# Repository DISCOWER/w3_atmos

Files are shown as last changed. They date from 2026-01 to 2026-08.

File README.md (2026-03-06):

---
layout: home
title: DISCOWER ATMOS
permalink: /
---

Welcome to the DISCOWER Autonomy Testbed for Multi-purpose Orbiting Systems (ATMOS) documentation page. 

ATMOS is a free-flyer platform developed at the KTH Space Robotics Laboratory for testing and validating space systems. The platform is composed by an air-bearing support system for frictionless motion, a modular actuation plate compatible with solenoid thrusters and propeller-based actuation, and a payload support system for testing various accessories. ATMOS aims at being a state-of-the-art platform for space robotics testing and validation, with the aim of reducing ground-to-orbit testing costs and increasing the reliability of space systems.

<html>
<script type="module" src="https://unpkg.com/@google/model-viewer/dist/model-viewer.min.js"></script>
<model-viewer src="/3D/full_assy_wAttachments.glb" 
              alt="A 3D model" 
              ar 
              auto-rotate 
              camera-controls 
              shadow-intensity="1">
</model-viewer>
<style>
    model-viewer {
        width: 100%;
        height: 500px;
        background-color: var(background-color, #ffffff);
    }
</style>
</html>

Here you can see the 3D platform used in DISCOWER. In this website, we provide detailed setups on assembling such a free-flyer platform, including modular actuation plates and payload bays.

> ##### ATMOS in Augmented Reality
>
> Visualizing this website on Android allows you to see ATMOS in Augmented Reality. Just click the AR button on the 3D model above!
{: .block-tip }

### Changelog
The latest changes to the documentation can be found below:
- **2026-03-06**: 
  - Added MIT and UIUC to ATMOS-supported institutions
  - Updated Bill-of-Materials part 0212 with the correct version of the Festo Push-in T-connector (QSMT-6 instead of QST-6)
- **2026-02-19**:
  - Contributions from Caltech (Vivian Norum and Teagan Abeling) and MIT (Kareena Shah and Brooke Schmelz): 
    - Updated regulator part number for thruster module.
    - Updated baseplate aluminum profile height from 21cm to 23cm for extra clearance for thicker bottles
    - Added missing item on BOM (air-bearing to push-in tubing adapter)
- **2025-01-15**:
  - ATMOS website is now open-source! Feel free to send in Pull-Requests with updates to the documentation at [https://github.com/DISCOWER/w3_atmos](https://github.com/DISCOWER/w3_atmos)

- **2025-11-24**: 
  - Updated Jetson Box STL files in [Avionics Plate](https://atmos.discower.io/jekyll/2024-11-23-avionics.html#onboard-computer) to match latest version of ATMOS
  - Added aluminium profile height for each layer in [Base Plate](https://atmos.discower.io/jekyll/2024-11-21-baseplate.html#pneumatic-plate---attached), [Actuation Plate](http://127.0.0.1:4000/jekyll/2024-11-22-actuation.html#aluminium-profiles), and [Avionics Plate](https://atmos.discower.io/jekyll/2024-11-23-avionics.html#payload-aluminium-profiles)
  - Updated PX4 instructions in [Pixhawk Setup](https://atmos.discower.io/pages/PX4/) for the multiple connection options with UXRCE and MAVLink

## Citing this work

A preprint with information regarding ATMOS and the KTH Space Robotics Laboratory is [available on arXiv](https://arxiv.org/abs/2501.16973), with the latest version being published in [IEEE Transactions on Field Robotics](https://ieeexplore.ieee.org/document/11245595). If this work is useful for your research, consider citing:

```bibtex
@ARTICLE{11245595,
  author={Roque, Pedro and Phodapol, Sujet and Krantz, Elias and Lim, Jaeyoung and Verhagen, Joris and Jiang, Frank J. and Dörner, David and Mao, Huina and Tibert, Gunnar and Siegwart, Roland and Stenius, Ivan and Tumova, Jana and Fuglesang, Christer and Dimarogonas, Dimos V.},
  journal={IEEE Transactions on Field Robotics}, 
  title={Toward Open-Source and Modular Space Systems With ATMOS}, 
  year={2026},
  volume={3},
  number={},
  pages={141-161},
  keywords={Space vehicles;Robots;Hardware;Floors;Testing;Aerospace electronics;Attitude control;Orbits;MATLAB;Propulsion;Multirobot systems;orbital robotics},
  doi={10.1109/TFR.2025.3632772}}
```
<html>
<iframe src="https://drive.google.com/file/d/1IQ3zcbxwNgNY_v_4YbrNEkiCZEV_he8L/preview" width="100%" height="435" allow="autoplay"></iframe>
</html>

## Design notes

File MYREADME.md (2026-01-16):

# platform
This repository provides an open-source free-flyer platform for testing satellite-like dynamics in ground testbeds.

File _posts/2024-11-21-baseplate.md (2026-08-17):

---
title: Base Plate
author: Pedro Roque
date: 2024-11-21
category: Jekyll
layout: post
---

To assemble a free-flyer, we will start with the bottom plate. This plate provides support for the remaining layers and contains the pneumatic components for air-supply, regulation, as well as air bearings for frictionless motion. The final assembly can be seen in the 3D model below.

<html>

<script type="module" src="https://unpkg.com/@google/model-viewer/dist/model-viewer.min.js"></script>
<model-viewer src="/3D/1. Bottom Plate/1_f.glb" 
              alt="Bottom plate" 
              ar 
              auto-rotate 
              camera-controls 
              shadow-intensity="1">
</model-viewer>
<style>
    model-viewer {
        width: 100%;
        height: 500px;
        background-color: var(background-color, #ffffff);
    }
</style>
</html>

## Polycarbonate Plate

The baseplate is composed of a single 8 mm thick polycarbonate plate - item 0101 in the Bill of Materials. The diameter of the plate is 400mm and it is recommended to be cut using a CNC waterjet. The DXF file for the plate can be downloaded [here](/dxf/base_plate.DXF), and the end result can be seen in the 3D model below.

<html>
<script type="module" src="https://unpkg.com/@google/model-viewer/dist/model-viewer.min.js"></script>
<model-viewer src="/3D/1. Bottom Plate/1_a.glb" 
              alt="Bottom plate - PC" 
              ar 
              auto-rotate 
              camera-controls 
              shadow-intensity="1">
</model-viewer>
<style>
    model-viewer {
        width: 100%;
        height: 500px;
        background-color: var(background-color, #ffffff);
    }
</style>
</html>

<div style="display: table; width: 300px; margin: 20px auto; border: 2px solid #000000; padding: 10px; text-align: center; background-color: var(background-color, #ffffff); border-radius: 4px;">
  Download the <a href="/dxf/base_plate.DXF" download>DXF file</a>.
</div>

## Air Bearings

With the plate cut, we are ready to start attaching the air bearings. These bearings are used to provide a frictionless motion to the platform. The bearings are attached to the plate using the provided mounting screws, nuts and washers - items 0103 and 0104. In the center of the plate, on the underside, we should also attach an X-connecting piece to allow for the air supply to reach the bearings - item 0214. Then, connect the air bearings to the X-connector using 6mm tubing - item 0210. A further length of tubing runs from the X-connector up to the topside of the plate, where it connects to the air bearings regulator - item 0206 - in the step below. The 3D model below shows only the placement of the bearings and X-connector; the tubing runs and regulator (0206) not depicted.

<html>
<script type="module" src="https://unpkg.com/@google/model-viewer/dist/model-viewer.min.js"></script>
<model-viewer src="/3D/1. Bottom Plate/1_b.glb" 
              alt="Bottom plate - PC" 
              ar 
              auto-rotate 
              camera-controls 
              shadow-intensity="1">
</model-viewer>
<style>
    model-viewer {
        width: 100%;
        height: 500px;
        background-color: var(background-color, #ffffff);
    }
</style>
</html>

> ##### NOTE
>
> After installation, the air bearings shall be protected from damage and kept on clean surfaces.
> We recommend to use the provided boxes for storage and transportation.
{: .block-tip }

## Bottle Supports and Regulators

At this stage, we are ready to install the bottle supports, thruster pressure regulator, and air bearings regulator. The first step is to print all the 3D supports in [here](/stl/pneumatic_mount/base_plate_prints.zip). The parts are then attached to the plate using M4x20 mm screws, nuts and washers according to the 3D model below. The items used in this step are 0206, 0207, 0208. The air bearings regulator - item 0206 - takes the tubing run coming up from the X-connector beneath the plate. For the thruster pressure regulator - item 0207 - screw a push-in fitting - item 0208 - into the inlet and outlet ports and tighten each with a wrench before connecting any tubing; the G1/4 thread seals against the port face, and leaving these hand-tight is a common source of air leaks. The 6mm tubing then presses into the fittings by hand.

<html>
<script type="module" src="https://unpkg.com/@google/model-viewer/dist/model-viewer.min.js"></script>
<model-viewer src="/3D/1. Bottom Plate/1_c.glb" 
              alt="Bottom plate - PC" 
              ar 
              auto-rotate 
              camera-controls 
              shadow-intensity="1">
</model-viewer>
<style>
    model-viewer {
        width: 100%;
        height: 500px;
        background-color: var(background-color, #ffffff);
    }
</style>
</html>
<div style="display: table; width: 300px; margin: 20px auto; border: 2px solid #000000; padding: 10px; text-align: center; background-color: var(background-color, #ffffff); border-radius: 4px;">
  Download the <a href="/stl/pneumatic_mount/base_plate_prints.zip" download>STL files</a>.
</div>

## Bottles and in-line Regulators

Next, we are ready to test the bottles' mounting and install all in-line regulators. Start by taking one bottle (item 0201) and attach to it the first (item 0202) and second (item 0203) regulators. Then, at the end of the last regulator, make sure to use the provided Festo-compatible fitting. Lastly, attach the 3D print part that secures the regulators to the bottle next holder.

<html>
<script type="module" src="https://unpkg.com/@google/model-viewer/dist/model-viewer.min.js"></script>
<model-viewer src="/3D/1. Bottom Plate/1_d.glb" 
              alt="Bottom plate - PC" 
              ar 
              auto-rotate 
              camera-controls 
              shadow-intensity="1">
</model-viewer>
<style>
    model-viewer {
        width: 100%;
        height: 500px;
        background-color: var(background-color, #ffffff);
    }
</style>
</html>

## Aluminium Profiles

Almost at the last step, we are now ready to install the supporting aluminium profiles. These profiles are used to provide structural support to the platform and are attached to the plate using the provided angle brackets and T-slot nuts. The items used in this step are 0102, 0105, 0106. M4×8 mm screws and nuts are used to secure these items to the locations shown in the 3D model below. Attach the angle brackets - item 0105 - to the profiles first, working on a level surface: leave the T-slot nuts loose enough to slide, square everything up, then tighten evenly. Brackets set slightly off-square here will leave the profiles uneven once mounted to the polycarbonate plate.

<html>
<script type="module" src="https://unpkg.com/@google/model-viewer/dist/model-viewer.min.js"></script>
<model-viewer src="/3D/1. Bottom Plate/1_e.glb" 
              alt="Bottom plate - PC" 
              ar 
              auto-rotate 
              camera-controls 
              shadow-intensity="1">
</model-viewer>
<style>
    model-viewer {
        width: 100%;
        height: 500px;
        background-color: var(background-color, #ffffff);
    }
</style>
</html>

## Manifold

### Manifold - Assembly

At this point, we are ready to assemble the manifold plate that will direct the air from from the bottles to the air bearings and actuators. The STL files used in this step can be found below.

<html>
<script type="module" src="https://unpkg.com/@google/model-viewer/dist/model-viewer.min.js"></script>
<model-viewer src="/3D/3.1 Manifold/3_1_d.glb" 
              alt="Bottom plate - PC" 
              ar 
              auto-rotate 
              camera-controls 
              camera-orbit="180deg 75deg 3m" 
              shadow-intensity="1">
</model-viewer>
<style>
    model-viewer {
        width: 100%;
        height: 500px;
        background-color: var(background-color, #ffffff);
    }
</style>
</html>

<div style="display: table; width: 300px; margin: 20px auto; border: 2px solid #000000; padding: 10px; text-align: center; background-color: var(background-color, #ffffff); border-radius: 4px;">
  Download the <a href="/stl/control_panel/control_panel.zip" download>STL files</a>.
</div>

### Manifold - Baseplate

First, start by 3D printing the baseplate.

<html>
<script type="module" src="https://unpkg.com/@google/model-viewer/dist/model-viewer.min.js"></script>
<model-viewer src="/3D/3.1 Manifold/3_1_a.glb" 
              alt="Bottom plate - PC" 
              ar 
              auto-rotate 
              camera-controls 
              camera-orbit="180deg 75deg 3m" 
              shadow-intensity="1">
</model-viewer>
<style>
    model-viewer {
        width: 100%;
        height: 500px;
        background-color: var(background-color, #ffffff);
    }
</style>
</html>

### Manifold - Supports

Then, we attach the 3D printed supports for the valves and tubing using M3x8 mm screws and nuts.

<html>
<script type="module" src="https://unpkg.com/@google/model-viewer/dist/model-viewer.min.js"></script>
<model-viewer src="/3D/3.1 Manifold/3_1_b.glb" 
              alt="Bottom plate - PC" 
              ar 
              auto-rotate 
              camera-controls 
              camera-orbit="180deg 75deg 3m" 
              shadow-intensity="1">
</model-viewer>
<style>
    model-viewer {
        width: 100%;
        height: 500px;
        background-color: var(background-color, #ffffff);
    }
</style>
</html>

### Manifold - Valves, T-pieces and Tubing

Next, we attach the valves and T-pieces to the manifold plate using the valve supports. Note that the valves have a rectangle extrusion that will be used to attach to the support, ensuring correct orientation and alignment.

<html>
<script type="module" src="https://unpkg.com/@google/model-viewer/dist/model-viewer.min.js"></script>
<model-viewer src="/3D/3.1 Manifold/3_1_c.glb" 
              alt="Bottom plate - PC" 
              ar 
              auto-rotate 
              camera-controls 
              camera-orbit="180deg 75deg 3m" 
              shadow-intensity="1">
</model-viewer>
<style>
    model-viewer {
        width: 100%;
        height: 500px;
        background-color: var(background-color, #ffffff);
    }
</style>
</html>

Lastly, we can add the tubing to the manifold.

<html>
<script type="module" src="https://unpkg.com/@google/model-viewer/dist/model-viewer.min.js"></script>
<model-viewer src="/3D/3.1 Manifold/3_1_d.glb" 
              alt="Bottom plate - PC" 
              ar 
              auto-rotate 
              camera-controls 
              camera-orbit="180deg 75deg 3m" 
              shadow-intensity="1">
</model-viewer>
<style>
    model-viewer {
        width: 100%;
        height: 500px;
        background-color: var(background-color, #ffffff);
    }
</style>
</html>

## Pneumatic Plate - Attached

The last component to attach to the baseplate is the manifold plate. This plate is used to provide a mounting location for the valves that direct the airflow. The aluminium profiles are then attached to the base plate using M4x20 mm screws T-slot nuts - item 0106. Each aluminum profile should have a length of 23cm. Using 6mm tubing (item 0210), connect the bottles to the pneumatic plate according to the diagram. Print the provided 3D parts and assemble them according to the 3D model below.

<html>
<script type="module" src="https://unpkg.com/@google/model-viewer/dist/model-viewer.min.js"></script>
<style>
    model-viewer {
        width: 100%;
        height: 500px;
        background-color: var(background-color, #ffffff);
    }
    .hotspot{
    display: block;
    width: 20px;
    height: 20px;
    border-radius: 10px;
    border: none;
    background-color: blue;
    box-sizing: border-box;
    pointer-events: none;
  }
  .hotspot[slot="hotspot-hand"]{
    --min-hotspot-opacity: 0;
    background-color: red;
  }
  .annotation{
    background-color: #888888;
    position: absolute;
    transform: translate(10px, 10px);
    border-radius: 10px;
    padding: 10px;
  }
  /* This keeps child nodes hidden while the element loads */
  :not(:defined) > * {
    display: none;
  }
</style>
<model-viewer src="/3D/1. Bottom Plate/1_f.glb" 
              alt="Bottom plate" 
              ar 
              camera-controls 
              shadow-intensity="1">
    <button class="hotspot" slot="hotspot-frombottle1" data-position="0.075 0.223 -0.15" data-normal="0 0 -1">
         <div class="annotation">From bottle 1.</div>
    </button>
    <button class="hotspot" slot="hotspot-frombottle2" data-position="0.075 0.195 -0.15" data-normal="0 0 -1">
         <div class="annotation">From bottle 2.</div>
    </button>
    <button class="hotspot" slot="hotspot-frombottle3" data-position="0.075 0.169 -0.15" data-normal="0 0 -1">
         <div class="annotation">From bottle 3.</div>
    </button>
    <button class="hotspot" slot="hotspot-actuation" data-position="0.065 0.135 -0.15" data-normal="0 0 -1">
         <div class="annotation">To actuation regulator (A)</div>
    </button>
    <button class="hotspot" slot="hotspot-bearings" data-position="0.065 0.11 -0.15" data-normal="0 0 -1">
         <div class="annotation">To air-bearing regulator (B)</div>
    </button>
    <button class="hotspot" slot="hotspot-bottle1" data-position="0.17 0.10 0.06" data-normal="0 0 1">
         <div class="annotation">Bottle 1.</div>
    </button>
    <button class="hotspot" slot="hotspot-bottle3" data-position="0.17 0.10 -0.06" data-normal="0 0 1">
         <div class="annotation">Bottle 3.</div>
    </button>
    <button class="hotspot" slot="hotspot-bottle2" data-position="-0.17 0.195 0.0" data-normal="0 0 1">
         <div class="annotation">Bottle 2.</div>
    </button>
    <button class="hotspot" slot="hotspot-reg-in" data-position="-0.035 0.075 0.16" data-normal="0 0 1">
         <div class="annotation">From manifold (A)</div>
    </button>
    <button class="hotspot" slot="hotspot-reg-out" data-position="0.035 0.075 0.16" data-normal="0 0 1">
         <div class="annotation">To actuation plate</div>
    </button>
    <button class="hotspot" slot="hotspot-bearing-reg-in" data-position="0.017 0.06 -0.16" data-normal="0 0 -1">
         <div class="annotation">From manifold (B)</div>
    </button>
    <button class="hotspot" slot="hotspot-bearing-reg-out" data-position="-0.017 0.06 -0.16" data-normal="0 0 -1">
         <div class="annotation">To air-bearing plate</div>
    </button>
</model-viewer>
</html>

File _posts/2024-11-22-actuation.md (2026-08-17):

---
title: Actuation Plate
author: Pedro Roque
date: 2024-11-22
category: Jekyll
layout: post
---

The second layer in the free-flyer is the actuation plate, a modular component that provides thruster capabilities via solenoid valves, but which can also be switched for other actuator models such as. Below, you can see the 3D model of the actuation plate with 8 thrusters, two in each thruster module. Each module houses two solenoid valves, that will be later controlled by the onboard PX4.

<html>

<script type="module" src="https://unpkg.com/@google/model-viewer/dist/model-viewer.min.js"></script>
<model-viewer src="/3D/2. Middle Plate/2_d.glb" 
              alt="Bottom plate" 
              ar 
              auto-rotate 
              camera-controls 
              shadow-intensity="1">
</model-viewer>
<style>
    model-viewer {
        width: 100%;
        height: 500px;
        background-color: var(background-color, #ffffff);
    }
</style>
</html>

## Actuation Support Plate (Middle Plate)

First, start by cutting with a water jet the actuation support plate, item 0201 in the Bill of Materials. The plate is 8mm thick and has a diameter of 400mm. The DXF file for the plate can be downloaded [here](/dxf/middle_plate.DXF), and the end result can be seen in the 3D model below.

<html>
<script type="module" src="https://unpkg.com/@google/model-viewer/dist/model-viewer.min.js"></script>
<model-viewer src="/3D/2. Middle Plate/2_a.glb" 
              alt="Bottom plate" 
              ar 
              auto-rotate 
              camera-controls 
              shadow-intensity="1">
</model-viewer>
<style>
    model-viewer {
        width: 100%;
        height: 500px;
        background-color: var(background-color, #ffffff);
    }
</style>
</html>
<div style="display: table; width: 300px; margin: 20px auto; border: 2px solid #000000; padding: 10px; text-align: center; background-color: var(background-color, #ffffff); border-radius: 4px;">
  Download the <a href="/dxf/middle_plate.DXF" download>DXF file</a>.
</div>

## Actuation Plate

Then, we can waterjet the actuation plate that will host the thrusters. The DXF file for it can be downloaded below. The actuation plate is attached to the middle plate using 8 standoffs, item 0107, and 8 M5×20 mm screws. The assembly can be seen in the 3D model below.

<html>
<script type="module" src="https://unpkg.com/@google/model-viewer/dist/model-viewer.min.js"></script>
<model-viewer src="/3D/2. Middle Plate/2_b.glb" 
              alt="Bottom plate" 
              ar 
              auto-rotate 
              camera-controls 
              shadow-intensity="1">
</model-viewer>
<style>
    model-viewer {
        width: 100%;
        height: 500px;
        background-color: var(background-color, #ffffff);
    }
</style>
</html>
<div style="display: table; width: 300px; margin: 20px auto; border: 2px solid #000000; padding: 10px; text-align: center; background-color: var(background-color, #ffffff); border-radius: 4px;">
  Download the <a href="/dxf/actuation_plate.DXF" download>DXF file</a>.
</div>

## Thruster Modules

### Module Base

At this stage, we are ready to assemble the thruster modules. We will provide instructions for one such module, knowing that the procedure can be repeated for the other three. Note that the actuation modules are 2 original format and 2 mirrored units. To start, print the housings provided with the link below.

<html>
<script type="module" src="https://unpkg.com/@google/model-viewer/dist/model-viewer.min.js"></script>
<model-viewer src="/3D/3. Thruster Modules/3_a.glb" 
              alt="Bottom plate" 
              ar 
              auto-rotate 
              camera-controls 
              shadow-intensity="1">
</model-viewer>
<style>
    model-viewer {
        width: 100%;
        height: 500px;
        background-color: var(background-color, #ffffff);
    }
</style>
</html>

<div style="display: table; width: 500px; margin: 20px auto; border: 2px solid #000000; padding: 10px; text-align: center; background-color: var(background-color, #ffffff); border-radius: 4px;">
  Download the <a href="/stl/actuator_module/actuator_mount_bottom.STL" download>Original</a> and <a href="/stl/actuator_module/mirror_actuator_mount_bottom.STL" download>Mirrored</a> STLs.
</div>

### First Solenoid

Then, we can install the first solenoid with the 4-to-2mm adapter, as well as the 2mm tubing (items 0209, 0211, 0216). Airflow through this solenoid (item 0209) is non-reversible — verify input/output orientation before installing. The solenoid is attached to the housing using the provided 3D printed part that is secured with M2x8 mm screws. The assembly can be seen in the 3D model below.

<html>
<script type="module" src="https://unpkg.com/@google/model-viewer/dist/model-viewer.min.js"></script>
<model-viewer src="/3D/3. Thruster Modules/3_b.glb" 
              alt="Bottom plate" 
              ar 
              auto-rotate 
              camera-controls 
              shadow-intensity="1">
</model-viewer>
<style>
    model-viewer {
        width: 100%;
        height: 500px;
        background-color: var(background-color, #ffffff);
    }
</style>
</html>
<div style="display: table; width: 500px; margin: 20px auto; border: 2px solid #000000; padding: 10px; text-align: center; background-color: var(background-color, #ffffff); border-radius: 4px;">
  Download the <a href="/stl/actuator_module/actuator_mount_holder.STL" download>solenoid holder</a> and the <a href="/stl/actuator_module/actuator_mount_nozzle_holder.STL" download>nozzle holder</a>.
</div>

### Second Solenoid

Then, we can install the second solenoid, on top of the first one, as shown in the visualization below. The items used are 0209, 0211, and 0216. The solenoid is attached to the housing using the provided 3D printed part that is secured with M2x8 mm screws. The assembly can be seen in the 3D model below. 

<html>
<script type="module" src="https://unpkg.com/@google/model-viewer/dist/model-viewer.min.js"></script>
<model-viewer src="/3D/3. Thruster Modules/3_c.glb" 
              alt="Bottom plate" 
              ar 
              auto-rotate 
              camera-controls 
              shadow-intensity="1">
</model-viewer>
<style>
    model-viewer {
        width: 100%;
        height: 500px;
        background-color: var(background-color, #ffffff);
    }
</style>
</html>
<div style="display: table; width: 500px; margin: 20px auto; border: 2px solid #000000; padding: 10px; text-align: center; background-color: var(background-color, #ffffff); border-radius: 4px;">
  Download the <a href="/stl/actuator_module/actuator_mount_holder_top.STL" download>solenoid holder</a> and the <a href="/stl/actuator_module/actuator_mount_nozzle_holder.STL" download>nozzle holder</a>.
</div>

### Power and Signal Distribution PCB

Now we are ready to install the power and signal distribution PCB on the side of the thruster module, as shown below. The PCB is composed of items 0010 and 0011. The PCB is attached to the housing using 2 M2x10 mm screws and nuts. Add M2 washers to offset the PCB from the housing. The assembly can be seen in the 3D model below.

<html>
<script type="module" src="https://unpkg.com/@google/model-viewer/dist/model-viewer.min.js"></script>
<model-viewer src="/3D/3. Thruster Modules/3_d.glb" 
              alt="Bottom plate" 
              ar 
              auto-rotate 
              camera-controls 
              shadow-intensity="1">
</model-viewer>
<style>
    model-viewer {
        width: 100%;
        height: 500px;
        background-color: var(background-color, #ffffff);
    }
</style>
</html>

The pictures below show the PCB's front and back, as well as the schematic view.
<html>
<a>
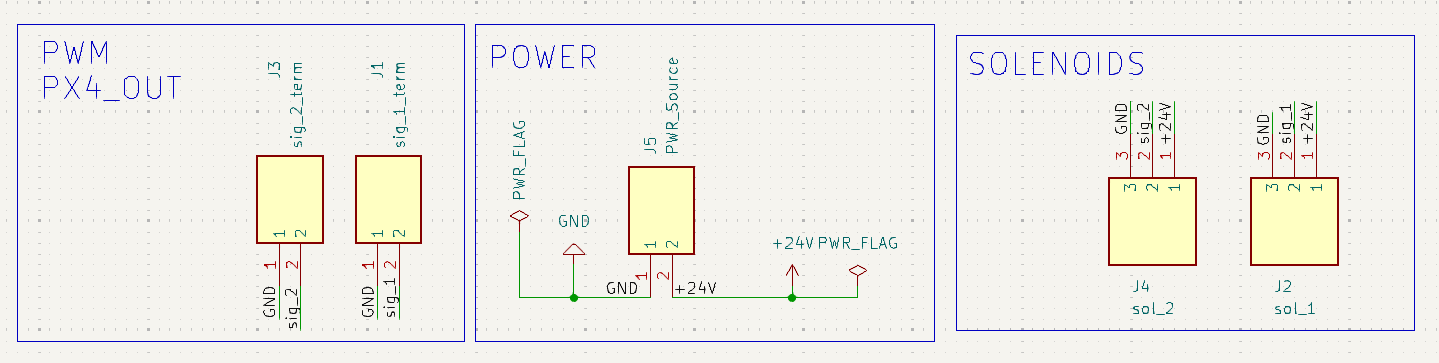
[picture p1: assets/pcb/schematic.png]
Schematic
     
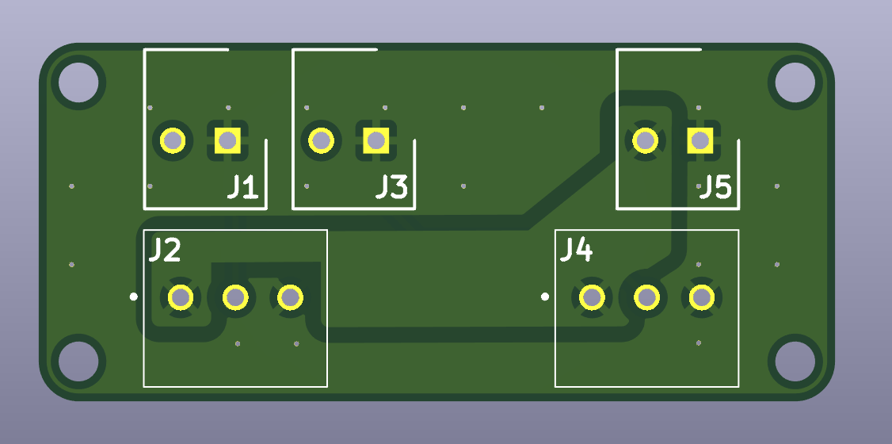
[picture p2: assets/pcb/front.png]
     
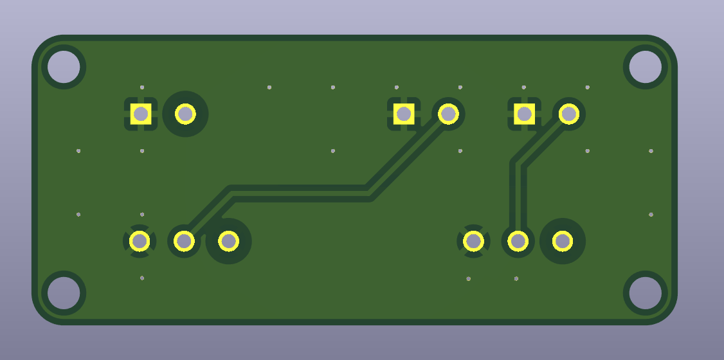
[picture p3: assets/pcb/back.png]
     
</a>
<style>
    model-viewer {
        width: 100%;
        height: 500px;
        background-color: var(background-color, #ffffff);
    }
</style>
</html>

> ##### Gerber Files
>
> Gerber files for this PCB will soon be made available for easy fabrication.
{: .block-tip }

### Power Regulator and Top Cover

With the bottom part finished, we can now install the power regulator on the top cover. The power regulator is item 0003 and it is attached to the top cover (3D printed with the STL below) with two M4x8 mm screws and nuts. The assembly can be seen in the 3D model below.

<html>
<script type="module" src="https://unpkg.com/@google/model-viewer/dist/model-viewer.min.js"></script>
<model-viewer src="/3D/3. Thruster Modules/3_e.glb" 
              alt="Bottom plate" 
              ar 
              auto-rotate 
              camera-controls 
              shadow-intensity="1">
</model-viewer>
<style>
    model-viewer {
        width: 100%;
        height: 500px;
        background-color: var(background-color, #ffffff);
    }
</style>
</html>

<div style="display: table; width: 500px; margin: 20px auto; border: 2px solid #000000; padding: 10px; text-align: center; background-color: var(background-color, #ffffff); border-radius: 4px;">
  Download the <a href="/stl/actuator_module/actuator_mount_top.STL" download>Original</a> and <a href="/stl/actuator_module/mirroractuator_mount_top.STL" download>Mirrored</a> STLs.
</div>

### Thruster Module Assembly

The last step is to attach the top cover using M3x8 mm screws and nuts, as per the assembly below.

<html>
<script type="module" src="https://unpkg.com/@google/model-viewer/dist/model-viewer.min.js"></script>
<model-viewer src="/3D/3. Thruster Modules/3_f.glb" 
              alt="Bottom plate" 
              ar 
              auto-rotate 
              camera-controls 
              shadow-intensity="1">
</model-viewer>
<style>
    model-viewer {
        width: 100%;
        height: 500px;
        background-color: var(background-color, #ffffff);
    }
</style>
</html>

### Thruster Module Wiring

After assembling each thruster module, the next step is to connect the power regulator and the thrusters' solenoids to the on-board PCB and the Pixhawk's PWM breakout board.  

The power regulator provides a stable 24V output for the thruster solenoids and other module electronics. It has four wires, connected as:  
**Input (9-40 V)**: Connect to the main power source.  
**Input GND**: Connect to the main supply ground.  
**Output (+24 V, 6 A)**: Provides regulated 24V to the thruster PCB. Connect to J5.  
**Output GND**: Provides ground reference to the thruster PCB. Connect to J5.  
_Here, Input and Output refer to the input and output of the power regulator._

Each thruster (T1-T8) is connected to a corresponding pair of terminals on the PCB, which then routes the signal to the Pixhawk PWM breakout board. The table below summarizes the thruster wiring.

| **Thruster** | **Module** | **Force Direction**\* | **PCB Connections** |
|---|---|---|---|
| **T1** | M1 | +X | Solenoid → J2 → J1 → **PWM1** |
| **T2** | M2 | -X | Solenoid → J4 → J3 → **PWM2** |
| **T3** | M3 | +X | Solenoid → J4 → J3 → **PWM3** |
| **T4** | M4 | -X | Solenoid → J2 → J1 → **PWM4** |
| **T5** | M2 | +Y | Solenoid → J2 → J1 → **PWM5** |
| **T6** | M4 | -Y | Solenoid → J4 → J3 → **PWM6** |
| **T7** | M1 | +Y | Solenoid → J4 → J3 → **PWM7** |
| **T8** | M3 | -Y | Solenoid → J2 → J1 → **PWM8** |

\*_Direction using the coordinate frame of the Pixhawk controller, i.e. X-forward, Y-right, Z-down._

Below 3D view illustrates each thruster (T1-T8) and thruster module (M1-M4). Refer to it for correct placement, orientation and wiring.

<html>
<script type="module" src="https://unpkg.com/@google/model-viewer/dist/model-viewer.min.js"></script>
<style>
    model-viewer {
        width: 100%;
        height: 500px;
        background-color: var(background-color, #ffffff);
    }
    .hotspot{
    display: block;
    width: 20px;
    height: 20px;
    border-radius: 10px;
    border: none;
    background-color: blue;
    box-sizing: border-box;
    pointer-events: none;
  }
  .hotspot[slot="hotspot-hand"]{
    --min-hotspot-opacity: 0;
    background-color: red;
  }
  .annotation{
    background-color: #888888;
    position: absolute;
    transform: translate(10px, 10px);
    border-radius: 10px;
    padding: 10px;
  }
  /* This keeps child nodes hidden while the element loads */
  :not(:defined) > * {
    display: none;
  }
</style>
<model-viewer src="/3D/2. Middle Plate/2_c.glb" 
              alt="Bottom plate" 
              ar 
              camera-controls 
              shadow-intensity="1">
     <button class="hotspot" slot="hotspot-PWM-board" data-position="-0.01 0.33 0.021" data-normal="0 0 -1">
          <div class="annotation">PWM1-PWM8</div>
     </button>
         <button class="hotspot" slot="hotspot-module-1" data-position="-0.1 0.36 -0.1" data-normal="0 0 -1">
         <div class="annotation">M1</div>
    </button>
    <button class="hotspot" slot="hotspot-thruster-1" data-position="-0.08 0.3 -0.05" data-normal="0 0 -1">
         <div class="annotation">T1</div>
    </button>
    <button class="hotspot" slot="hotspot-thruster-7" data-position="-0.05 0.3 -0.08" data-normal="0 0 -1">
         <div class="annotation">T7</div>
    </button>
     <button class="hotspot" slot="hotspot-module-2" data-position="0.1 0.36 -0.1" data-normal="0 0 -1">
         <div class="annotation">M2</div>
    </button>
    <button class="hotspot" slot="hotspot-thruster-2" data-position="0.08 0.3 -0.05" data-normal="0 0 -1">
         <div class="annotation">T2</div>
    </button>
    <button class="hotspot" slot="hotspot-thruster-5" data-position="0.05 0.3 -0.08" data-normal="0 0 -1">
         <div class="annotation">T5</div>
    </button>
        <button class="hotspot" slot="hotspot-module-3" data-position="-0.1 0.36 0.1" data-normal="0 0 -1">
         <div class="annotation">M3</div>
    </button>
        <button class="hotspot" slot="hotspot-thruster-3" data-position="-0.08 0.3 0.05" data-normal="0 0 -1">
         <div class="annotation">T3</div>
    </button>
    <button class="hotspot" slot="hotspot-thruster-8" data-position="-0.05 0.3 0.08" data-normal="0 0 -1">
         <div class="annotation">T8</div>
    </button>
        <button class="hotspot" slot="hotspot-module-4" data-position="0.1 0.36 0.1" data-normal="0 0 -1">
         <div class="annotation">M4</div>
    </button>
        <button class="hotspot" slot="hotspot-thruster-4" data-position="0.08 0.3 0.05" data-normal="0 0 -1">
         <div class="annotation">T4</div>
    </button>
    <button class="hotspot" slot="hotspot-thruster-6" data-position="0.05 0.3 0.08" data-normal="0 0 -1">
         <div class="annotation">T6</div>
    </button>
</model-viewer>
</html>

## Actuator Plate and Pneumatic Connection

With all thruster modules assembled, it is time to install them on the plate and do all the power and pneumatic connections. For the pneumatic connections, please follow the diagram in the 3D model below, connecting the same letters to the same spots (that is A-A, B-B, etc). The power connections from the power regulators should be connected to the power hub in the actuation plate (item 0008) using power cables capable of passing a peak of 4A. Lastly, connect the PWM cables (item TODO) to the PX4 mini PWM receptor.

<html>
<script type="module" src="https://unpkg.com/@google/model-viewer/dist/model-viewer.min.js"></script>
<style>
    model-viewer {
        width: 100%;
        height: 500px;
        background-color: var(background-color, #ffffff);
    }
    .hotspot{
    display: block;
    width: 20px;
    height: 20px;
    border-radius: 10px;
    border: none;
    background-color: blue;
    box-sizing: border-box;
    pointer-events: none;
  }
  .hotspot[slot="hotspot-hand"]{
    --min-hotspot-opacity: 0;
    background-color: red;
  }
  .annotation{
    background-color: #888888;
    position: absolute;
    transform: translate(10px, 10px);
    border-radius: 10px;
    padding: 10px;
  }
  /* This keeps child nodes hidden while the element loads */
  :not(:defined) > * {
    display: none;
  }
</style>
<model-viewer src="/3D/2. Middle Plate/2_c.glb" 
              alt="Bottom plate" 
              ar 
              camera-controls 
              shadow-intensity="1">
    <button class="hotspot" slot="hotspot-from_manifold" data-position="0.055 0.295 0.0" data-normal="0 0 -1">
         <div class="annotation">From manifold</div>
    </button>
    <button class="hotspot" slot="hotspot-A_1" data-position="0.025 0.295 0.0" data-normal="0 0 -1">
         <div class="annotation">A</div>
    </button>
    <button class="hotspot" slot="hotspot-A_2" data-position="0.015 0.295 0.0" data-normal="0 0 -1">
         <div class="annotation">A</div>
    </button>
    <button class="hotspot" slot="hotspot-B_1" data-position="0.00 0.295 0.015" data-normal="0 0 -1">
         <div class="annotation">B</div>
    </button>
    <button class="hotspot" slot="hotspot-B_2" data-position="0.00 0.295 0.105" data-normal="0 0 -1">
         <div class="annotation">B</div>
    </button>
    <button class="hotspot" slot="hotspot-D1" data-position="-0.015 0.295 0.121" data-normal="0 0 -1">
         <div class="annotation">C</div>
    </button>
    <button class="hotspot" slot="hotspot-D2" data-position="-0.06 0.297 0.119" data-normal="0 0 -1">
         <div class="annotation">C</div>
    </button>
    <button class="hotspot" slot="hotspot-E1" data-position="0.015 0.295 0.121" data-normal="0 0 -1">
         <div class="annotation">D</div>
    </button>
    <button class="hotspot" slot="hotspot-E2" data-position="0.07 0.297 0.121" data-normal="0 0 -1">
         <div class="annotation">D</div>
    </button>
    <button class="hotspot" slot="hotspot-C1" data-position="0.00 0.295 -0.105" data-normal="0 0 -1">
         <div class="annotation">E</div>
    </button>
    <button class="hotspot" slot="hotspot-C2" data-position="0.00 0.295 -0.015" data-normal="0 0 -1">
         <div class="annotation">E</div>
    </button>
    <button class="hotspot" slot="hotspot-F1" data-position="-0.015 0.295 -0.121" data-normal="0 0 -1">
         <div class="annotation">F</div>
    </button>
    <button class="hotspot" slot="hotspot-F2" data-position="-0.06 0.297 -0.119" data-normal="0 0 -1">
         <div class="annotation">F</div>
    </button>
    <button class="hotspot" slot="hotspot-G1" data-position="0.015 0.295 -0.121" data-normal="0 0 -1">
         <div class="annotation">G</div>
    </button>
    <button class="hotspot" slot="hotspot-G2" data-position="0.07 0.297 -0.121" data-normal="0 0 -1">
         <div class="annotation">G</div>
    </button>
    <button class="hotspot" slot="hotspot-H1" data-position="0.04 0.295 0.015" data-normal="0 0 -1">
         <div class="annotation">H</div>
    </button>
    <button class="hotspot" slot="hotspot-H2" data-position="-0.055 0.31 0.015" data-normal="0 0 -1">
         <div class="annotation">H</div>
    </button>
    <button class="hotspot" slot="hotspot-I1" data-position="-0.07 0.31 0.0" data-normal="0 0 -1">
         <div class="annotation">I</div>
    </button>
    <button class="hotspot" slot="hotspot-I2" data-position="-0.105 0.31 0.0" data-normal="0 0 -1">
         <div class="annotation">I</div>
    </button>
    <button class="hotspot" slot="hotspot-J1" data-position="-0.12 0.31 -0.015" data-normal="0 0 -1">
         <div class="annotation">J</div>
    </button>
    <button class="hotspot" slot="hotspot-J2" data-position="-0.12 0.31 -0.06" data-normal="0 0 -1">
         <div class="annotation">J</div>
    </button>
    <button class="hotspot" slot="hotspot-K1" data-position="-0.12 0.31 0.015" data-normal="0 0 -1">
         <div class="annotation">K</div>
    </button>
    <button class="hotspot" slot="hotspot-K2" data-position="-0.12 0.31 0.06" data-normal="0 0 -1">
         <div class="annotation">K</div>
    </button>
    <button class="hotspot" slot="hotspot-L1" data-position="-0.044 0.31 0.0" data-normal="0 0 -1">
         <div class="annotation">L</div>
    </button>
    <button class="hotspot" slot="hotspot-L2" data-position="0.105 0.31 0.0" data-normal="0 0 -1">
         <div class="annotation">L</div>
    </button>
    <button class="hotspot" slot="hotspot-M1" data-position="0.12 0.31 0.015" data-normal="0 0 -1">
         <div class="annotation">M</div>
    </button>
    <button class="hotspot" slot="hotspot-M2" data-position="0.13 0.31 0.06" data-normal="0 0 -1">
         <div class="annotation">M</div>
    </button>
    <button class="hotspot" slot="hotspot-N1" data-position="0.12 0.31 -0.015" data-normal="0 0 -1">
         <div class="annotation">N</div>
    </button>
    <button class="hotspot" slot="hotspot-N2" data-position="0.13 0.31 -0.06" data-normal="0 0 -1">
         <div class="annotation">N</div>
    </button>
</model-viewer>
</html>

## Aluminium Profiles

Lastly, install the aluminium profiles in the middle plate. Each aluminium profile should have a lenght of 12cm. The profiles are attached to the plate using M4x20 mm screws and nuts. The assembly can be seen in the 3D model below- At this stage, your middle plate is complete.

<html>
<script type="module" src="https://unpkg.com/@google/model-viewer/dist/model-viewer.min.js"></script>
<model-viewer src="/3D/2. Middle Plate/2_d.glb" 
              alt="Bottom plate" 
              ar 
              auto-rotate 
              camera-controls 
              shadow-intensity="1">
</model-viewer>
<style>
    model-viewer {
        width: 100%;
        height: 500px;
        background-color: var(background-color, #ffffff);
    }
</style>
</html>

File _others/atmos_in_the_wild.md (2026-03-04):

---
title: ATMOS in the Wild
author: Pedro Roque
date: 2022-02-04
category: Jekyll
layout: post
---
<style>
.logo-track-wrap {
  overflow: hidden;
  width: 100%;
  margin: 0 0 30px;
  /* fade edges */
  -webkit-mask-image: linear-gradient(to right, transparent 0%, black 8%, black 92%, transparent 100%);
  mask-image: linear-gradient(to right, transparent 0%, black 8%, black 92%, transparent 100%);
}

.logo-track {
  display: flex;
  width: max-content;
  animation: logo-scroll 20s linear infinite;
}

.logo-track:hover {
  animation-play-state: paused;
}

@keyframes logo-scroll {
  0%   { transform: translateX(0); }
  100% { transform: translateX(-50%); }
}

.logo-item {
  display: flex;
  justify-content: center;
  align-items: center;
  height: 80px;
  width: 160px;
  padding: 10px 20px;
  flex-shrink: 0;
}

.logo-item img {
  max-height: 60px;
  max-width: 120px;
  width: auto;
  height: auto;
  object-fit: contain;
  /* opacity: 0.7; */
  transition: opacity 0.2s;
}

.logo-item img:hover {
  opacity: 1;
}
</style>

<!--
  Items are duplicated so the loop is seamless.
  animation translates by -50% (one full set), then snaps back to 0.
-->
<div class="logo-track-wrap">
  <div class="logo-track">
    <!-- original set -->
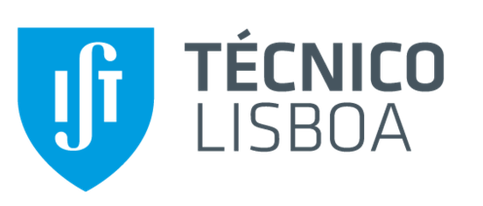
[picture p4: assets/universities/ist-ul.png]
IST
    
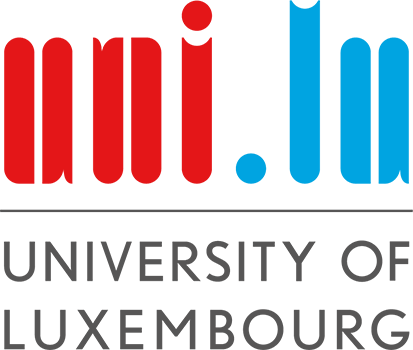
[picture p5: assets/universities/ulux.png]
ULUX
    
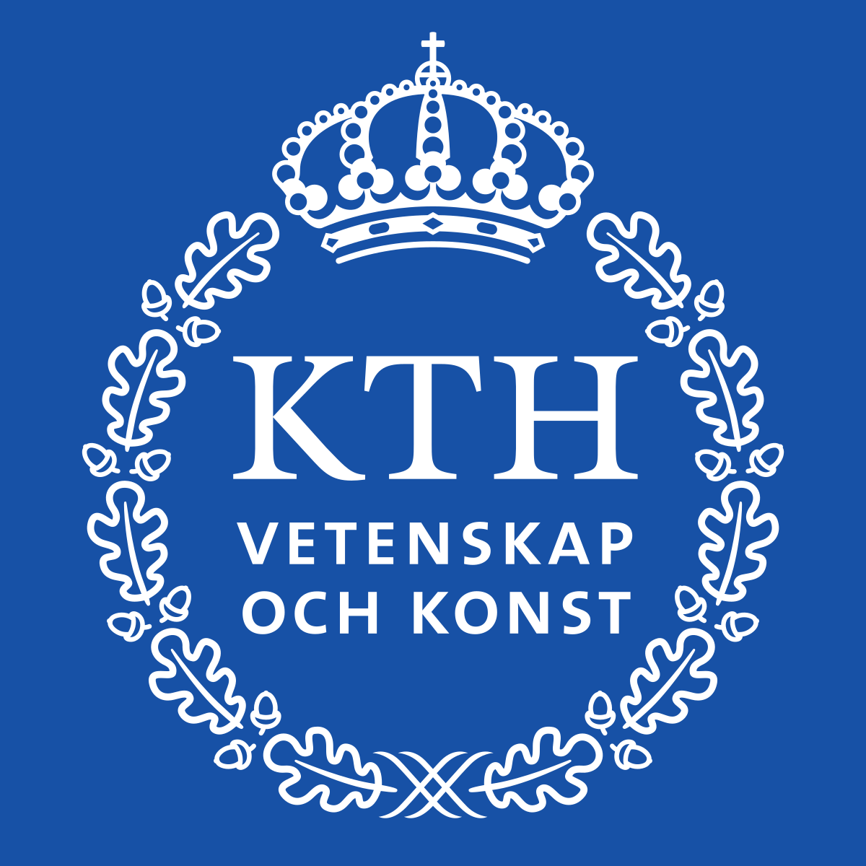
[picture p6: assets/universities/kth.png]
KTH
    
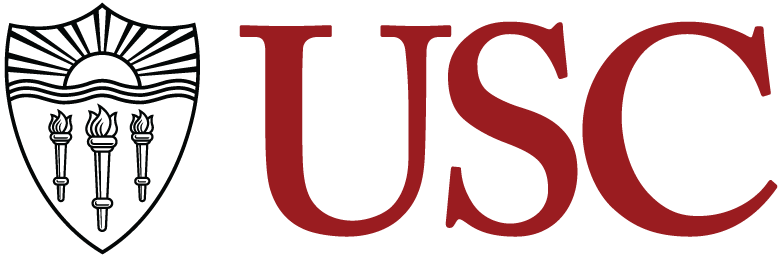
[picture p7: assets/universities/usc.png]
USC
    
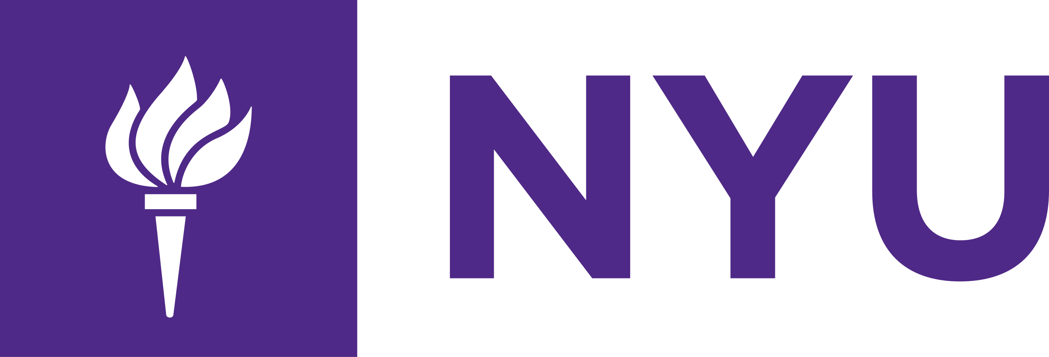
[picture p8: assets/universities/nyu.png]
NYU
    
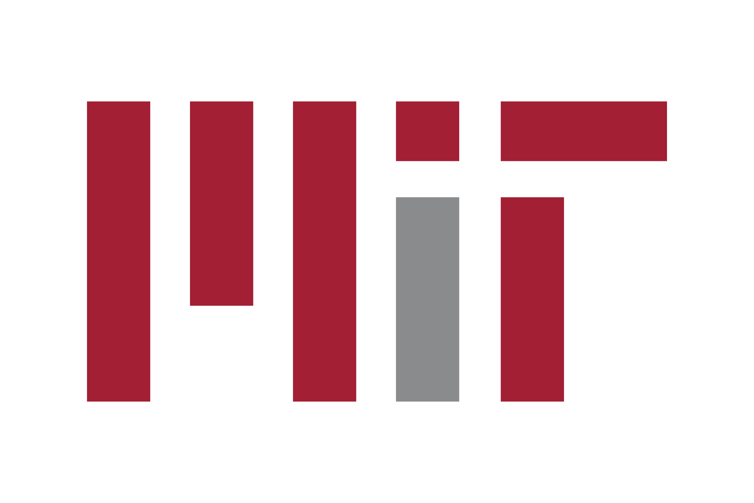
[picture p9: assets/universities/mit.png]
MIT
    
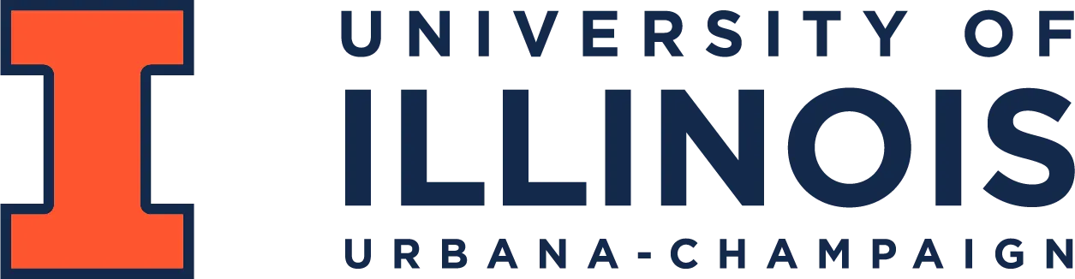
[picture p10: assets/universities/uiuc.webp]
UIUC
    
    <div class="logo-item">Icarus</div>
    <!-- duplicate set for seamless loop -->
    <div class="logo-item">IST</div>
    <div class="logo-item">ULUX</div>
    <div class="logo-item">KTH</div>
    <div class="logo-item">USC</div>
    <div class="logo-item">NYU</div>
    <div class="logo-item">MIT</div>
    <div class="logo-item">UIUC</div>
    <div class="logo-item">Icarus</div>
  </div>
</div>

On this page, you find a collection of laboratories using ATMOS and/or PX4Space. Below you can see the platforms used in each laboratory.

## KTH Royal Institute of Technology
At KTH's Space Robotics Laboratory, ATMOS is the platform currently being used:

<script type="module" src="https://unpkg.com/@google/model-viewer/dist/model-viewer.min.js"></script>
<model-viewer src="/3D/full_assy_wAttachments.glb" 
              alt="A 3D model" 
              ar 
              auto-rotate 
              camera-controls 
              shadow-intensity="1">
</model-viewer>

<style>
model-viewer { width: 100%; height: 500px; background-color: var(background-color, #ffffff); }
</style>

## University of Southern California
At USC's Laboratory for Autonomous Systems in Exploration and Robotics (LASER) led by [Keenan Albee](https://albee.github.io), starting in Summer 2025, ATMOS will be used for multi-agent controls:

<script type="module" src="https://unpkg.com/@google/model-viewer/dist/model-viewer.min.js"></script>
<model-viewer src="/3D/full_assy.glb" 
              alt="A 3D model" 
              ar 
              auto-rotate 
              camera-controls 
              shadow-intensity="1">
</model-viewer>

<style>
model-viewer { width: 100%; height: 500px; background-color: var(background-color, #ffffff); }
</style>

## New York University
At NYU's Riviere Robot Lab (RRL) led by [Ben Riviere](https://sites.google.com/view/riviere-robot-lab/home), starting in Autumn 2025, ATMOS will be used for multi-agent controls and artificial intelligence research:

<script type="module" src="https://unpkg.com/@google/model-viewer/dist/model-viewer.min.js"></script>
<model-viewer src="/3D/full_assy.glb" 
              alt="A 3D model" 
              ar 
              auto-rotate 
              camera-controls 
              shadow-intensity="1">
</model-viewer>

<style>
model-viewer { width: 100%; height: 500px; background-color: var(background-color, #ffffff); }
</style>

## Massachusetts Institute of Technology
At MIT's Astrodynamics, Space Robotics, and Controls Lab [(ARCLab)](https://aeroastro.mit.edu/arclab/) led by [Richard Linares](https://aeroastro.mit.edu/people/richard-linares/), ATMOS will be used for astrodynamics and controls research:

<script type="module" src="https://unpkg.com/@google/model-viewer/dist/model-viewer.min.js"></script>
<model-viewer src="/3D/full_assy.glb" 
              alt="A 3D model" 
              ar 
              auto-rotate 
              camera-controls 
              shadow-intensity="1">
</model-viewer>

<style>
model-viewer { width: 100%; height: 500px; background-color: var(background-color, #ffffff); }
</style>

## University of Illinois Urbana-Champaign
At UIUC's Space Sustainability and Autonomy Lab [(SSA Lab)](https://lab.minduliw.com) led by the incoming [Minduli Wijayatunga](https://www.minduliw.com/), ATMOS will be used for developing intelligent and safe autonomy for space operations:

<script type="module" src="https://unpkg.com/@google/model-viewer/dist/model-viewer.min.js"></script>
<model-viewer src="/3D/full_assy.glb" 
              alt="A 3D model" 
              ar 
              auto-rotate 
              camera-controls 
              shadow-intensity="1">
</model-viewer>

<style>
model-viewer { width: 100%; height: 500px; background-color: var(background-color, #ffffff); }
</style>

## Icarus Robotics
At [Icarus Robotics](https://www.icarusrobotics.com/), the ATMOS base is used as a test platform for microgravity robotics, simulating the microgravity dynamics of Icarus free-flyer. Below, we show the base platform used by Icarus.

<script type="module" src="https://unpkg.com/@google/model-viewer/dist/model-viewer.min.js"></script>
<model-viewer src="/assets/universities/icarus.glb" 
              alt="A 3D model" 
              ar 
              auto-rotate 
              camera-controls 
              shadow-intensity="1">
</model-viewer>

<style>
model-viewer { width: 100%; height: 500px; background-color: var(background-color, #ffffff); }
</style>

## Instituto Superior Técnico - University of Lisbon
At IST's Institute for Systems and Robotics, the Space Cobot team led by [Rodrigo Ventura](https://wp.isr.tecnico.ulisboa.pt/rventura/) use PX4Space in the [Space Cobot](https://space-cobot.isr.tecnico.ulisboa.pt/) free-flyer:

<script type="module" src="https://unpkg.com/@google/model-viewer/dist/model-viewer.min.js"></script>
<model-viewer src="/assets/universities/Space Cobot.glb" 
              alt="A 3D model" 
              ar 
              auto-rotate 
              camera-controls
              camera-orbit="45deg 30deg 4m"
              shadow-intensity="1">
</model-viewer>

<style>
model-viewer { width: 100%; height: 500px; background-color: var(background-color, #ffffff); }
</style>

## University of Luxembourg
At UL's Interdisciplinary Centre for Security, Reliability and Trust (SnT), a modified ATMOS is used currently being built for microgravity research in the [SpaceR group](https://wwwen.uni.lu/snt/research/space_research_group), led by
[Miguel Olivares Mendez](https://www.uni.lu/snt-en/people/miguel-angel-olivares-mendez/):

<script type="module" src="https://unpkg.com/@google/model-viewer/dist/model-viewer.min.js"></script>
<model-viewer src="/assets/universities/ULXv2.glb" 
              alt="University of Luxembourg Platform" 
              ar 
              auto-rotate 
              camera-controls
              camera-orbit="10deg 60deg 2m"
              shadow-intensity="1">
</model-viewer>

<style>
model-viewer { width: 100%; height: 500px; background-color: var(background-color, #ffffff); }
</style>

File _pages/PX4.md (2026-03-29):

---
title: Pixhawk Setup
author: Elias Krantz
date: 2025-02-03
category: Jekyll
layout: post
---
This guide outlines the firmware setup process of the ATMOS Freeflyers' onboard microcontroller, the Pixhawk 6X Mini.

# PX4 Autopilot

We use PX4 Autopilot as the firmware for the Pixhawk 6X Mini, openly available here: [PX4 at GitHub](https://github.com/PX4/PX4-Autopilot). To begin, clone the PX4 repository to your local machine:

1. Clone the PX4 repository to your local machine:
   ```bash
   git clone git@github.com:PX4/PX4-Autopilot.git --recursive
   ```

2. Navigate to the cloned `PX4-Autopilot` directory and install the required packages:
   ```bash
   bash ./Tools/setup/ubuntu.sh
   ```
   After this step, rebooting your machine is recommended.

3. Build PX4 messages for ROS 2.  
   To communicate with the Pixhawk via ROS 2, you need its PX4 messages (available here: [PX4-msgs at GitHub](https://github.com/PX4/px4_msgs)) on your local machine.
   ```bash
   mkdir -p ~/px4_ws/src/
   cd ~/px4_ws/src/
   git clone git@github.com:PX4/px4_msgs.git
   cd ~/px4_ws
   colcon build
   source install/setup.bash 
   ```

4. Configure PX4 topics for ROS 2.  
   The ROS 2 topics PX4 publishes (`fmu/out/`) and subscribes to (`fmu/in/`) are defined by `dds_topics.yaml` in the `PX4-Autopilot` directory. We recommend replacing this file with our version before firmware installation.  
   Download ATMOS' [dds_topics.yaml](/assets/px4_autopilot/dds_topics.yaml) and replace the ones found at `PX4-Autopilot/src/modules/uxrce_dds_client/dds_topics.yaml`.

## Firmware Installation

To upload the PX4 firmware to the Pixhawk controller:

1. Connect the Pixhawk to your computer via serial.
2. Navigate to the cloned `PX4-Autopilot` directory.
3. Upload the firmware using:

```bash
make px4_fmu-v6x_spacecraft upload
```

## Setting a Default Namespace

We recommend setting a default ROS 2 namespace for PX4 using the `PX4_UXRCE_DDS_NS` parameter. Specify it during firmware upload:

```bash
PX4_UXRCE_DDS_NS=<namespace> make px4_fmu-v6x_spacecraft upload
```

# Vehicle Configuration and QGroundControl

QGroundControl is the ground control station used to interface with PX4 from a local machine. It is openly available here: [QGroundControl at GitHub](https://github.com/mavlink/qgroundcontrol).

> ##### QGround Control Version
>
> Until the spacecraft feature is available in QGroundControl stable releases, we recommend using the latest daily build version available here: [QGroundControl Daily Builds](https://docs.qgroundcontrol.com/master/en/qgc-user-guide/releases/daily_builds.html#daily-builds).
{: .block-tip }

## Setting up QGroundControl

To build QGroundControl for Linux Ubuntu, you first need:
```bash
sudo usermod -a -G dialout $USER
sudo apt-get remove modemmanager -y
sudo apt install gstreamer1.0-plugins-bad gstreamer1.0-libav gstreamer1.0-gl -y
sudo apt install libfuse2 -y
sudo apt install libxcb-xinerama0 libxkbcommon-x11-0 libxcb-cursor-dev -y
```

Logout and login again to enable the change to user permissions.

After downloading QGroundControl, make it executable:
```bash
chmod +x ./QGroundControl-x86_64.AppImage
```

To launch it, simply run:
```bash
./QGroundControl-x86_64.AppImage
```

## PX4 Vehicle Setup

Once QGroundControl is installed, follow these steps:

1. **Connect the Pixhawk to QGroundControl**
   - Open QGroundControl and connect the Pixhawk to configure the PX4.
   - Navigate to **Vehicle Setup**.

2. **Calibrate the RC (First-time Setup)**
   - Go to Airframe and select **Spacecraft** as the vehicle type, followed by "KTH ATMOS Freeflyer". QGroundControl will prompt you to reboot PX4.
   - Go to the **Radio** tab and follow the calibration procedure.
   - Go to the **Flight Modes** tab and assign flight modes to RC switches:
     - One switch for ARMING/DISARMING.
     - One for MANUAL/ACRO/POSITION.
     - One for OFFBOARD ON/OFF. 

3. **PX4 IP Setup**:
   - In QGroundControl, navigate to **Analyze Tools -> MAVLink Console**.
   - Set PX4 IP address **in MAVLink Console** with:
      ```bash
      echo DEVICE=eth0 > /fs/microsd/net.cfg
      echo BOOTPROTO=fallback >> /fs/microsd/net.cfg
      echo IPADDR=192.168.0.10 >> /fs/microsd/net.cfg
      echo NETMASK=255.255.255.0 >>/fs/microsd/net.cfg
      echo ROUTER=192.168.0.254 >>/fs/microsd/net.cfg
      echo DNS=192.168.0.254 >>/fs/microsd/net.cfg
      ```
   - Reboot the PX4 controller to apply the settings.
      - Either power cycle the Pixhawk or reboot it via **Vehicle Setup -> Parameters -> Tools -> Reboot Vehicle**.

   - In **MAVLink Console**, verify that the IP is set correctly after reboot:
      ```bash
      netman showw
      ```
      Once completed, PX4 should be ready to communicate with the onboard computer.

4. **Configure Parameters**
   - Go to the **Parameters** tab.
   - UXRCE DDS Configuration:
     The PX4 runs a UXRCE-DDS client to expose local UORB topics to the ROS 2 environment.
     - First, ensure that UXRCE runs on boot by ensuring that the parameter `UXRCE_DDS_CFG` is set to `Ethernet` (ATMOS with Pixhawk 6X uses Ethernet), in case you are using an ethernet connection between PX4 and the onboard computer. If using serial communication, set it to the corresponding serial configuration for your board.
      - **For Ethernet-connected Pixhawk**: Next we need to ensure that UXRCE-DDS can connect to the onboard computer IP address. This is controlled with the parameter `UXRCE_DDS_AG_IP` via an integer value. We are using `192.168.0.1`, which is mapped to `-1062731775`. Set this parameter to the agent's IP mapping. For other mappings, run:
         ```bash
         python3 Tools/convert_ip.py "<IP-address>"
         ```
      - **For Serial-connected Pixhawk**: Set the parameter `UXRCE_DDS_CFG` to the corresponding serial configuration for your board. Then, select the serial port and baudrate parameters (`SER_{port}_BAUD`). Higher baudrate settings are recommended for better performance (e.g., 921600 or higher), but may degrade performance on longer/poor cabling. Also ensure that Mavlink over serial is disabled on the selected port by checking that `MAV_{0,1,2}_CONFIG` are set to a different serial port than `UXRCE_DDS_CFG` or `Disabled`.

    - MAVLink Configuration:
      ATMOS uses MAVLink over USB to provide an interface to the ground control station / QGroundControl. To use this functionality, ensure that the following parameters are set:
         - `SYS_USB_AUTO` is set to `Auto-detect` or `MAVLink`.
         - If using multiple ATMOS, assign each PX4 controller a unique MAVLink system ID using the `MAV_SYS_ID` parameter.

    - Reboot the PX4 controller
       - Either power cycle the Pixhawk or reboot it via **Parameters -> Tools -> Reboot Vehicle**.

# PX4 Setup Completed

Now we are ready to set up the Nvidia Jetson Orin NX. Please proceed to the next page.

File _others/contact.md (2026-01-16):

---
title: Contact Us
author: Pedro Roque
date: 2022-02-05
category: Jekyll
layout: post
---

In case you have any questions regarding the platform, files, or integration, feel free to drop us a message on our Discord channel. We will be glad to help you out. 

Click the image below to join us on Discord!

<div style="width: 50%; margin-left: auto; margin-right: auto; padding-top: 25px;">
<a href="https://discord.gg/gqN4qnuRUP">
    DISCOWER ATMOS Discord
</a>
</div>

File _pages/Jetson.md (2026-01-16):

---
title: Onboard Computer Setup
author: Pedro Roque
date: 2025-02-04
category: Jekyll
layout: post
---
Setup routine and scripts for the ATMOS free-flyers' onboard computers (OBC). For ATMOS, we consider the NVIDIA Jetson Orin NX as the OBC, but these instructions can be roughly follower for other Ubuntu 22.04 OBCs.

# Jetson Setup

These instructions assume that the Jetson is running Ubuntu 22.04 on Jetpack 6. Then, install ROS 2 Humble:

1. Follow installation instructions at https://docs.ros.org/en/humble/Installation/Ubuntu-Install-Debians.html

2. Source ROS 2 by default

   ```bash
   echo "source /opt/ros/humble/setup.bash" >> ~/.bashrc
   ```

Lastly, clone:
```bash
git clone git@github.com:DISCOWER/FF_OBC_Setup.git $HOME/FF_OBC_Setup
```

If cloning fails due to SSH authentication, make sure the OBC has GitHub SSH keys configured. See [GitHub's guide](https://docs.github.com/en/authentication/connecting-to-github-with-ssh/generating-a-new-ssh-key-and-adding-it-to-the-ssh-agent) to generating SSH keys for instructions.

# Set the hostname

1. Change the hostname by replacing `<hostname>` with the desired name.
   ```bash
   sudo hostnamectl set-hostname <hostname>
   ```
2. Edit the /etc/hosts file.
   ```bash
   sudo vim /etc/hosts
   ```
   Find the line that starts with 127.0.0.1 or 127.0.1.1 followed by the old hostname (probably discower) and change it to the new hostname. Save and close the file.

# Set up ROS 2 Workspace

Here we provide an example of a workspace setup for the PX4 communication and the vehicle's odometry. Note that our interface was tested on a Qualisys motion capture setup using the repository in `https://github.com/DISCOWER/motion_capture_system`. For motion capture systems with different coordinates, you may need to adjust the `srl_vehicle_mocap_odom` package.

1. Set up workspace. Clone and build required ROS 2 packages. 
   ```bash
   mkdir -p ~/atmos_ws/src/
   cd ~/atmos_ws/src/
   git clone git@github.com:PX4/px4_msgs.git
   git clone git@github.com:DISCOWER/srl_vehicle_mocap_odom.git
   cd ~/atmos_ws
   colcon build
   ```

# Install Micro-XRCE-DDS-Agent
Install with snap-store
```bash
sudo snap install micro-xrce-dds-agent --edge
```

Set up Micro-XRCE-DDS-Agent as a service:
```bash
sudo snap set micro-xrce-dds-agent daemon=true
sudo snap set micro-xrce-dds-agent transport=udp4
sudo snap set micro-xrce-dds-agent port=8888
sudo systemctl enable snap.micro-xrce-dds-agent.daemon.service
```

For Serial Communication: for serial communication between PX4 and the onboard computer, change the transport to serial and set the corresponding parameters:
```bash
sudo snap set micro-xrce-dds-agent daemon=true
sudo snap set micro-xrce-dds-agent transport=serial
sudo snap set micro-xrce-dds-agent device=<obc-serial-port>
sudo snap set micro-xrce-dds-agent baudrate=<your-baudrate-from-PX4>
sudo systemctl enable snap.micro-xrce-dds-agent.daemon.service
```

# Add PX4 Rules for USB Mavlink interface

These rules assume that the PX4 is connected via USB to the onboard computer. To add the udev rules, run:

```bash
sudo cp $HOME/FF_OBC_Setup/rules/* /etc/udev/rules.d/
sudo udevadm control --reload-rules
sudo udevadm trigger
```

# Add MAVProxy and Mavlink Router

Follow these instructions to install the mavlink-router:
```bash
sudo apt install git meson ninja-build pkg-config gcc g++ systemd
sudo pip3 install meson
git clone git@github.com:mavlink-router/mavlink-router.git ~/mavlink_router
cd ~/mavlink_router
git submodule update --init --recursive
meson setup build .
sudo ninja -C build install
sudo mkdir -p /etc/mavlink-router/
sudo cp $HOME/FF_OBC_Setup/mavlink.conf/* /etc/mavlink-router/
```

# Add the startup service

These services will auto-start the motion capture odometry node and the mavlink-router on boot. Note that the **ROS2 node in** `srl_vehicle_mocap_odom` **might require modifications** for your application and laboratory setup.

```bash
sudo cp $HOME/FF_OBC_Setup/services/* /etc/systemd/system/
sudo systemctl daemon-reload
sudo systemctl enable vehicle_mocap_odom
sudo systemctl start vehicle_mocap_odom
sudo systemctl enable mavlink-router
sudo systemctl start mavlink-router
```

# Add a Static IP for the PX4 Ethernet

Set a static IP-address for the PX4 ethernet connection. This is done via **NetworkManager** on the onboard computer. We are using `192.168.0.1`.

1. Open a terminal and check existing network connections:

   ```bash
   nmcli connection show
   ```

   Identify the connection used for the PX4.

2. Open the connection’s configuration file in a text editor:

   ```bash
   sudo vim /etc/NetworkManager/system-connections/<your-wired-connection>.nmconnection
   ```

   Replace `<your-wired-connection>` with the actual connection name.

3. Modify the configuration file to set a static IP. The settings should include:

   ```
   [connection]
   id=<your-wired-connection>
   uuid=<generated-uuid>
   type=ethernet

   [ipv4]
   address1=192.168.0.1/24,192.168.0.254
   method=manual

   [ipv6]
   addr-gen-mode=stable-privacy
   method=auto
   ```

4. Save the file and restart **NetworkManager**:

   ```bash
   sudo systemctl restart NetworkManager
   ```

# All set!

At this point, you can reboot the system and the services should start automatically. You can check if all ROS 2 topics are available with:
```bash
ros2 topic list
```

The FMU topics should be populated. You can check if the communication is successful by subscribing to vehicle_attitude:
```bash
ros2 topic echo /fmu/out/vehicle_attitude
```

Lastly, on the Ground Control Station (a personal laptop, for instance), open QGroundControl, add a TCP Comm Link to the IP of the vehicle (leave the port as default) and check for connection. QGroundControl should report the vehicle status.

<!-- # Optional: Set up SAM gripper

2. Add the startup service

   ```bash
   sudo cp /home/discower/FF_OBC_Setup/services/gripper_comm.service /etc/systemd/system/
   sudo systemctl daemon-reload
   sudo systemctl enable gripper_comm
   sudo systemctl start gripper_comm
   ```
 -->

<!-- # Setup WiFi 7 - Intel BE200

1. Install `iwlwifi-modules` with
   ```bash
   sudo apt install -y iwlwifi-modules
   ```
2. Setup boot support for the module
   ```bash
   echo iwlwifi | sudo tee -a /etc/modules
   ``` -->

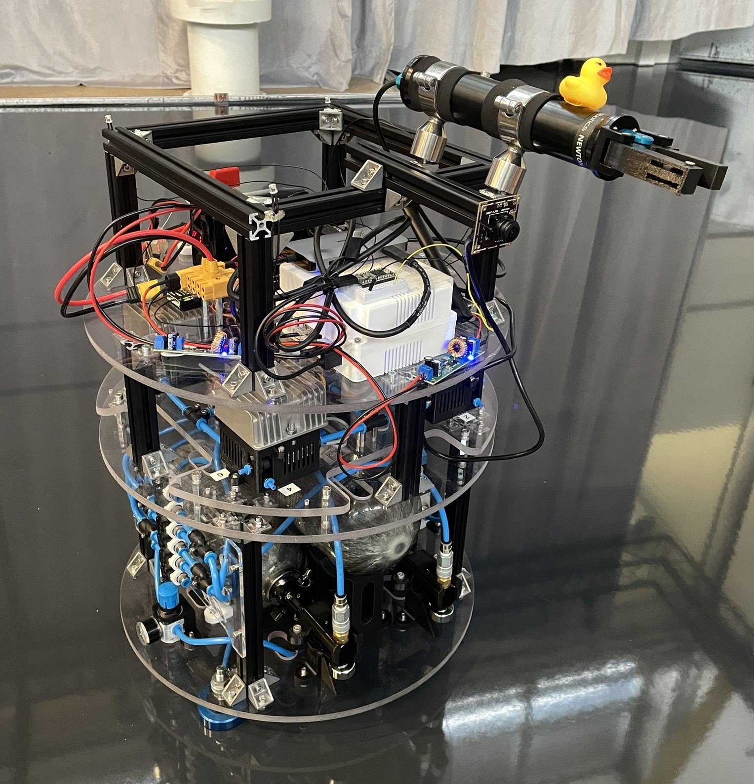
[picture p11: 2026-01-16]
figures/platform.jpg

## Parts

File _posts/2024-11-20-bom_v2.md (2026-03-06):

---
title: Bill of Materials (BOM)
author: Pedro Roque
date: 2024-10-28
category: Jekyll
layout: post
---

In this page we provide a list of materials used in the construction of the DISCOWER Freeflyer platform. The list is divided into three categories: Electronics, Mechanical, and Pneumatics. The list is not exhaustive and may be updated as the project progresses. In case you find any missing information or have any questions, please contact us.

**Approximate cost:** 7000 EUR

| Part No. | Name | Description |
|:---|:---|:---|
| | **Electronics** | |
| 0001 | [NVIDIA Orin Jetson NX](https://www.nvidia.com/en-us/autonomous-machines/embedded-systems/jetson-orin/) | Onboard computer. There exist different options for carrier boards. |
| 0001a | [Connect Tech Boson Carrier Board](https://connecttech.com/product/boson-for-framos-carrier-board-for-nvidia-jetson-orin-nx/) | Carrier board for NVIDIA Orin Jetson NX |
| 0001b | [Ugreen USB Hub (2 USB-A and 2 USB-C)](https://www.teknikdelar.se/produkt/ugreen-hub-usb-c-till-2x-usb-a-2-x-usb-c-20cm-gra) | USB-C hub |
| 0001c | [Intel 8265NGW WiFi Card](https://www.fruugo.se/dual-mode-ac8265-wireless-nic-module-support-24ghz5ghz-wifi-and-bluetooth-42-for-nano-kit/p-260936901-570900391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) | WiFi 802.11ac/a/b/g/n card for Jetson Orin NX |
| 0001d | [Kingston 500GB SSD](https://www.webhallen.com/se/product/353791-Kingston-NV2-M-2-500GB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) | SSD for storing the Operating System - other M2 NVMe should also be compatible |
| 0002 | [Pixhawk 6X Mini](https://holybro.com/products/pixhawk-6x?variant=44399078768829) | Low-level controller |
| 0003 | [Buck Boost DC-DC Converter to 24V >100W](https://a.co/d/hgXubyN) | DC/DC converter for thruster solenoid valves. Requires at least 96W output at 24V.|
| 0004 | [Buck Converter Module, DC Voltage Step Down](https://amzn.eu/d/5HJ4z21) | Adjustable DC voltage regulator |
| 0005 | 6S Lipo Battery | 10Ah Lipo battery 6S with XT60 connector |
| 0006 | [On-Off Power Switch](https://se.rs-online.com/web/p/cam-switches/2714164) | Manual power switch |
| 0007 | XT60 Power Cables | Power Cables with XT60 connectors |
| 0008 | [XT60 Tarot Power Distribution Module](http://www.tarotrc.com/Product/Detail.aspx?Lang=en&Id=f6a32e2d-7978-4ef2-b018-ccd127e8c25d) | Power distribution module for XT60 |
| 0009 | [RC Receiver/Remote](https://docs.px4.io/main/en/getting_started/rc_transmitter_receiver.html) | RC receiver and remote compatible with PX4 |
| 0010  | [Adafruit Feather Proto](https://www.adafruit.com/product/2884) | PCB for Signal and Power Distribution |
| 0011  | [Wire-to-PCB Blocks](https://www.amazon.nl/-/en/YIXISI-Terminal-Connector-Mounting-Arduino/dp/B082ZNRQMJ?th=1) | Wire-to-PCB Blocks, 2P and 3P with 5mm pitch. |
| | **Mechanical** | |
| 0101 | [Polycarbonate plate, 8 mm thickness](https://se.rs-online.com/web/p/plastic-sheets/2586629) | Polycarbonate structural baseplates |
| 0102 | [Aluminium Profile, 20x20 mm with 5 mm groove](https://se.rs-online.com/web/p/tubing-and-profile-struts/8508489) | Aluminium strut profile structure |
| 0103 | [Ball Mounting Screws](https://www.newwayairbearings.com/catalog/product/13mm-diameter-ball-mounting-screws-round-end/) | Air bearing ball mounting screws 13 mm Dia. / M10x.75 x 54 mm, S8013B06  |
| 0104 | [Ball Retaining Clips](https://www.newwayairbearings.com/catalog/product/13mm-ball-retaining-clips/) | Air bearing 13 mm Ball retainer, S8013S01 |
| 0105 | [Angle Bracket, Strut Profile 20 mm](https://se.rs-online.com/web/p/connecting-components/1809136) | Angle bracket for strut profile 20 mm |
| 0106 | [M4 T-Slot Nut, Strut Profile 20 mm](https://se.rs-online.com/web/p/connecting-components/1809106) | M4 T-Slot Nut Connecting Component, Strut Profile 20 mm, Groove Size 5mm |
| 0107 | [Standoff, M5 Thread, 20mm](https://se.rs-online.com/web/p/standoffs/2053072) | Standoffs for baseplates |
| 0108 | Miscellanious screws, nuts and washers | Sizes M3, M4 and M5. Screws of lengths 8 mm, 16 mm, 20 mm, and 25 mm |
| | **Pneumatics** | |
| 0201 | [Dye Armotech Core Air Tank, 1.5 L](https://www.tacticalstore.se/en/brands/dye-paintball/dye-armotech-core-air-tank-1-5l-90-4500) | Air tanks of 1.5 L with 300 bar operating pressure |
| 0202 | [DYE LT Throttle Regulator 300 Bar](https://www.tacticalstore.se/en/paintball/air-systems-co2/regulators/dye-lt-throttle-regulator-300-bar-4500psi) | Air tank regulator, step 1, output 60 bar |
| 0202a | [Ninja Pro V3 4500PSI HP](https://www.tacticalstore.se/en/paintball/air-systems-co2/regulators/ninja-regulator-pro-v3-4500psi-hp/) | Alternative to 0202, better build quality but pricier. |
| 0203 | [Polarstar micro MR GEN2 Regulator](https://www.powair6.com/en/hpa-regulator/10928-polarstar-micro-mr-gen2-regulator.html) | Air tank regulator, step 2, adjustable output |
| 0204 | [Polarstar Male Quick Disconnect Fitting](https://polarstarairsoft.com/products/male-qd-fitting-assembly) | Fitting for Polarstar regulator |
| 0205 | [50 mm Flat Round Air Bearing](https://www.newwayairbearings.com/catalog/product/50mm-flat-round-air-bearings/) | Flat air bearings |
| 0206 | [Festo Pressure regulator MS2-LR-QS6-D6-AR-BAR-B](https://www.festo.com/se/en/a/8086638/) | Pressure regulator for air bearings |
| 0207 | [Festo Pressure regulator MS4-LR-1/4-D7-AS](https://www.festo.com/us/en/a/529419/) | Pressure regulator for thrusters |
| 0208 | [Festo Push-in fitting QS-G1/4-6](https://www.festo.com/us/en/a/186097/) | Push in fitting for regulator MS4-LR-1/4-D7-AS |
| 0209 | [Festo Solenoid Valve MHJ10-S-2,5-QS-6-HF](https://www.festo.com/tw/en/a/567503/) | Solenoid valve for thruster pulse control |
| 0210 | [Festo Plastic Tubing PEN-6X1-BL](https://www.festo.com/us/en/a/551457/) | 6/4 mm tubing |
| 0211 | [Legris Plastic Tubing 4 mm](https://se.rs-online.com/web/p/air-hoses/1447836) | 4/2 mm tubing for nozzles |
| 0212 | [Festo Push-in T-connector QSMT-6](https://www.festo.com/ee/en/a/153367/) | T-connector 6 mm |
| 0213 | [Festo Push-in Y-connector QSY-6](https://www.festo.com/us/en/a/153149/) | Y-connector 6 mm |
| 0214 | [Festo Push-in X-connector QSMX-6](https://www.festo.com/us/en/a/153380/) | X-connector 6 mm |
| 0215 | [Festo Ball Valve QH-QS-6](https://www.festo.com/us/en/a/153484/) | Manual shut-off valve |
| 0216 | [Festo Push-in connector QSM-6-4](https://www.festo.com/us/en/a/153327/) | 6 mm to 4 mm tubing connector |
| 0217 | [Festo Push-in connector QSM-M5-6-I](https://www.festo.com/us/en/a/153317/)| M5 thread to 6mm push-in tubing connector |

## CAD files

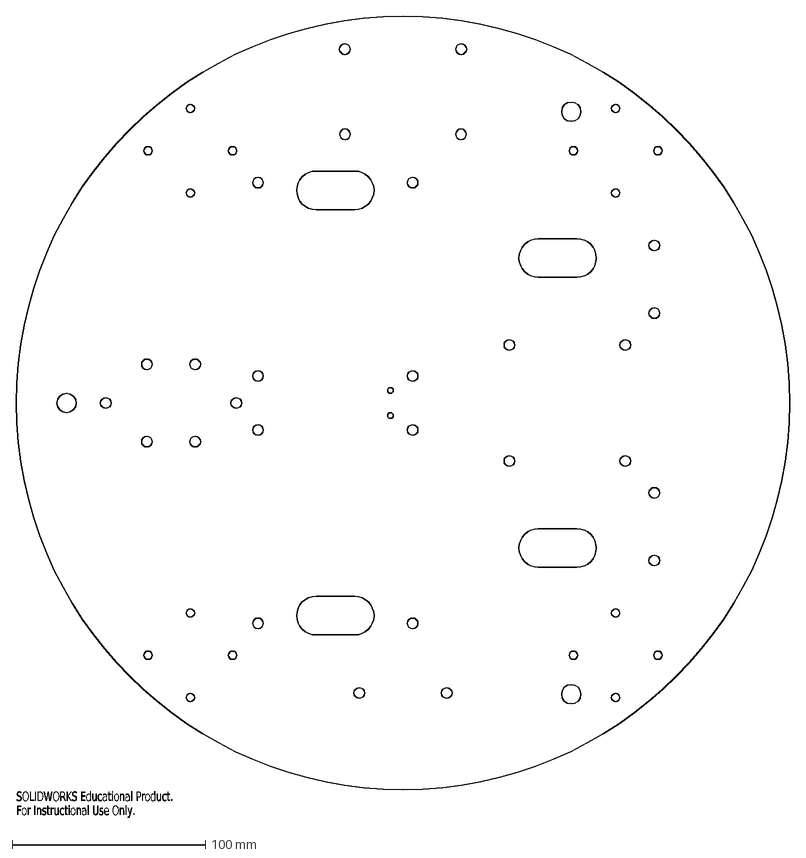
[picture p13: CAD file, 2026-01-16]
dxf/base_plate.DXF
SOLIDWORKS Educational Product.
For Instructional Use Only.

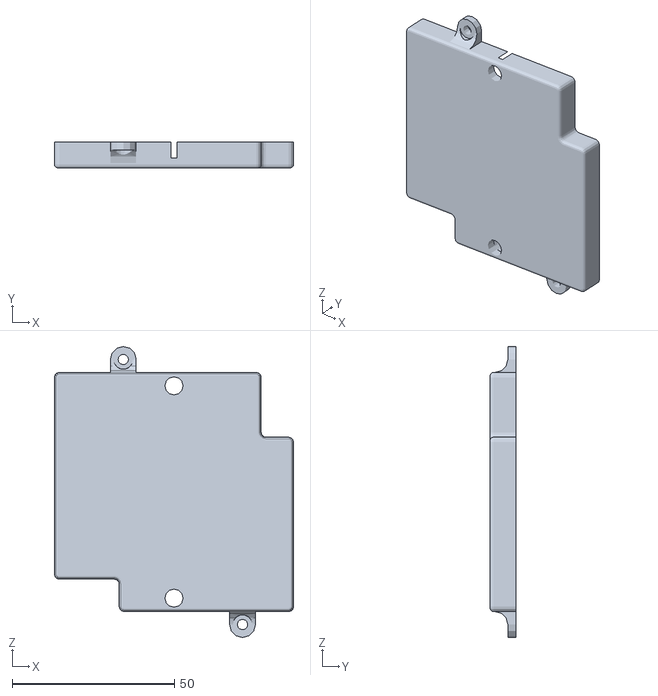
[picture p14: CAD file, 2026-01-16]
stl/actuator_module/mirroractuator_mount_top.STL
73.8 x 8.00 x 89.8

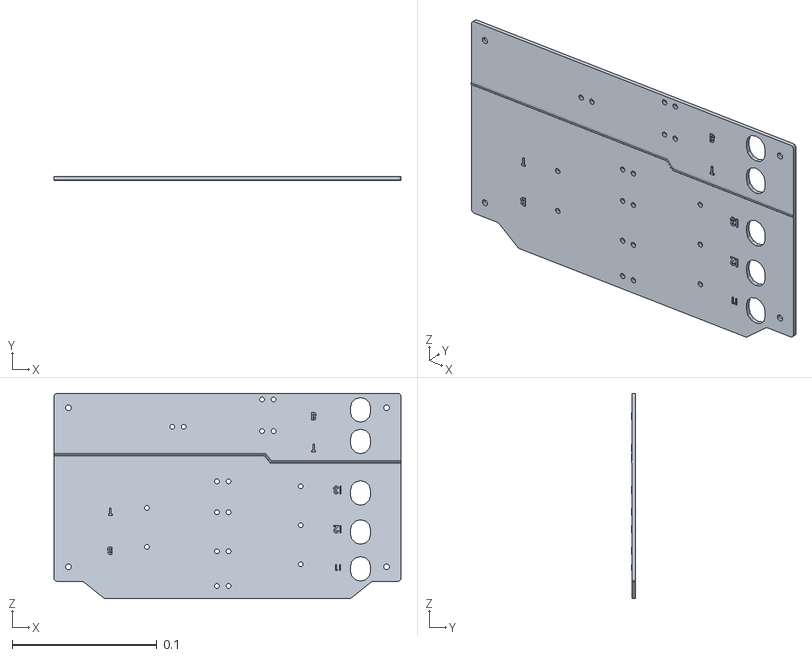
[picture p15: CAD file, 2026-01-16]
stl/control_panel/control_panel_mounting_plate.STL
0.24 x 0.003 x 0.142

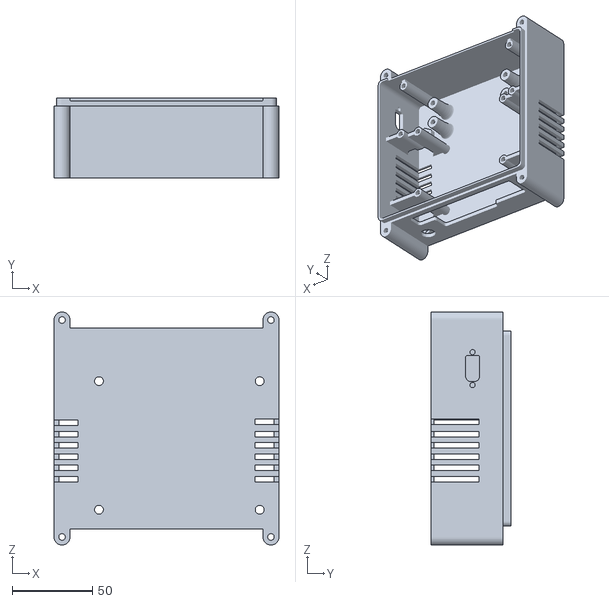
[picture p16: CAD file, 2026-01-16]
stl/electronics_plate/jetson_box_bottom.STL
140.0 x 50.0 x 145.0

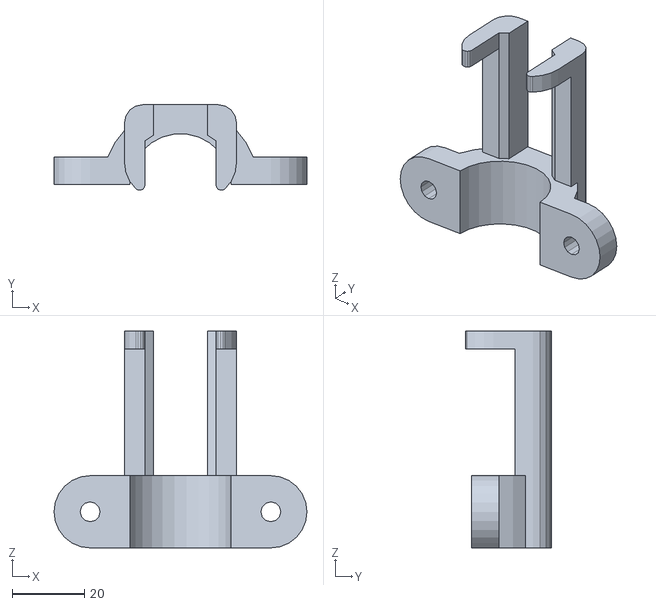
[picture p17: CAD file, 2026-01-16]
stl/pneumatic_mount/bottle_conncet_top.STL
70.0 x 23.7 x 60.0

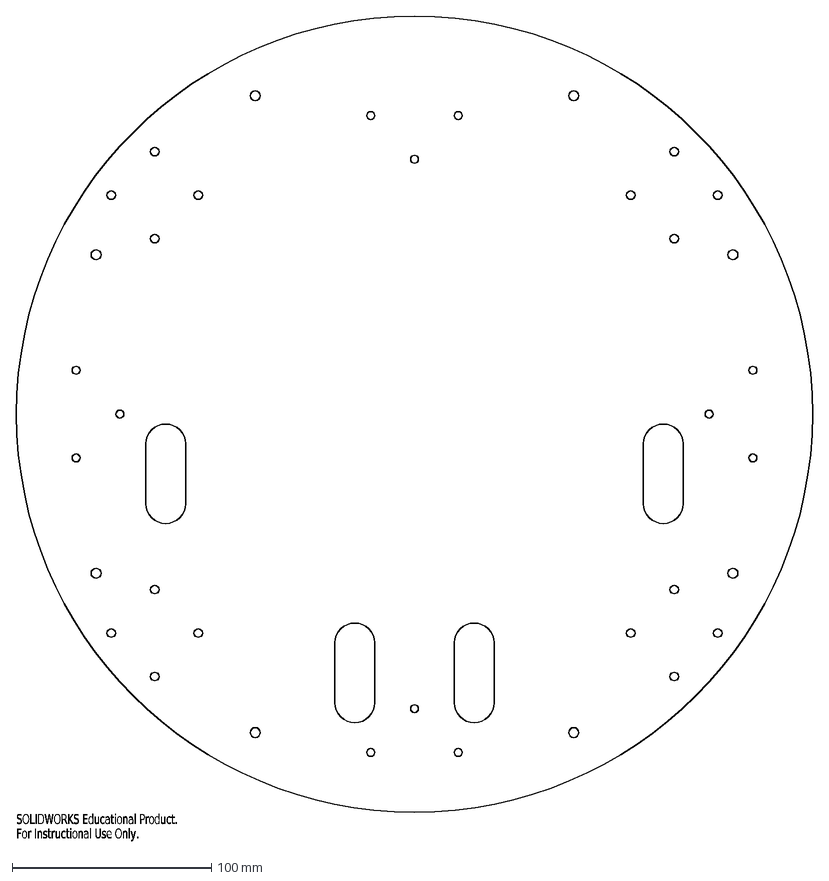
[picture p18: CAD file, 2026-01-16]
dxf/middle_plate.DXF
SOLIDWORKS Educational Product.
For Instructional Use Only.

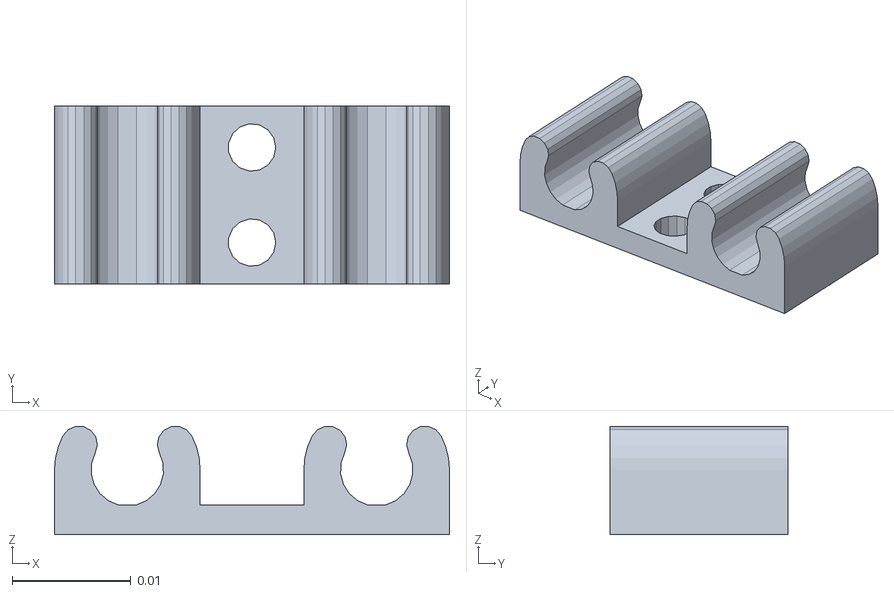
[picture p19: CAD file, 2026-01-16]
stl/control_panel/tube_mount.STL
0.0332 x 0.015 x 0.0091

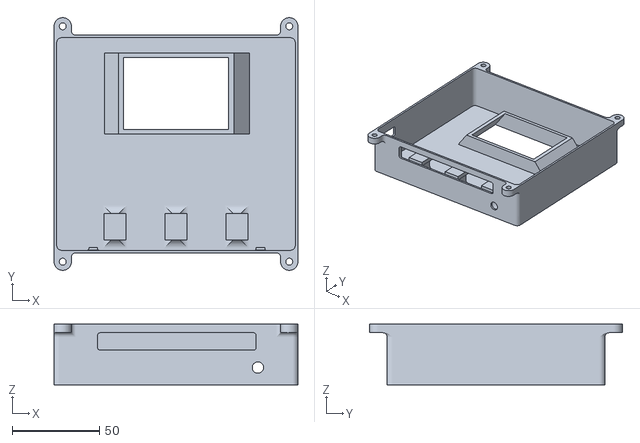
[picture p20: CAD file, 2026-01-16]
stl/electronics_plate/jetson_box_top.STL
140.0 x 145.0 x 35.0

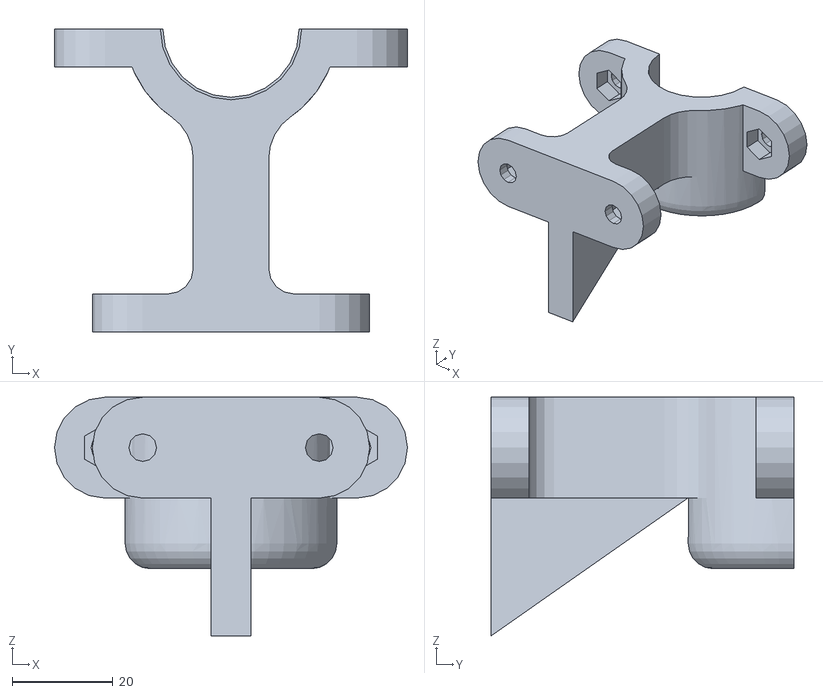
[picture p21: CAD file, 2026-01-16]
stl/pneumatic_mount/bottle_conncet_bot.STL
70.0 x 60.0 x 47.3

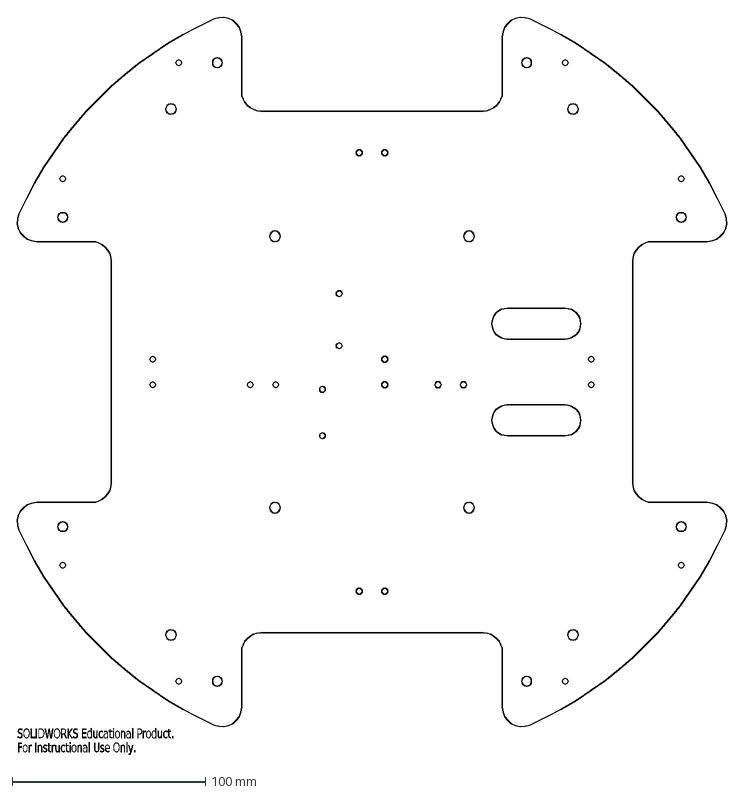
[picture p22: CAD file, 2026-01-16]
dxf/actuation_plate.DXF
SOLIDWORKS Educational Product.
For Instructional Use Only.

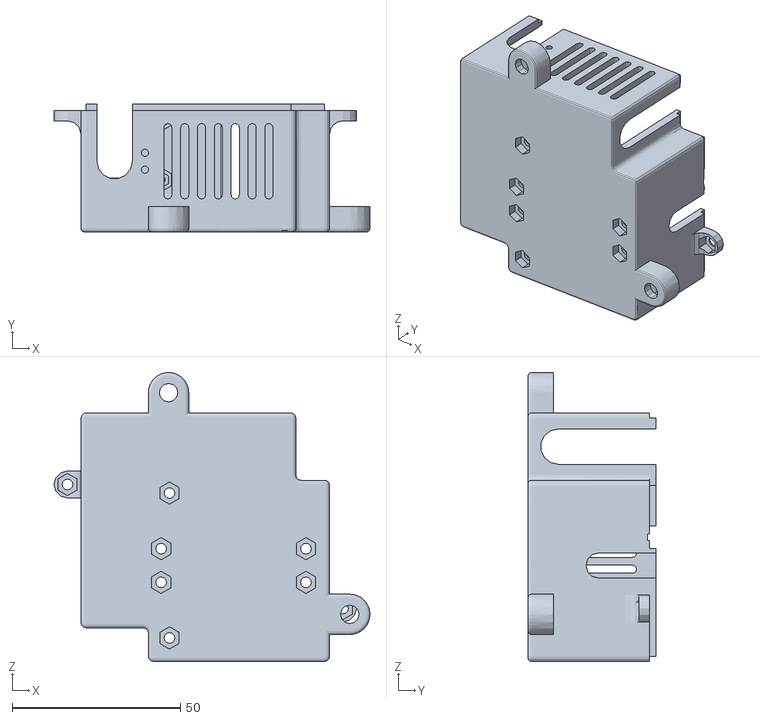
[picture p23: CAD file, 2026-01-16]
stl/actuator_module/mirror_actuator_mount_bottom.STL
93.8 x 38.0 x 85.8

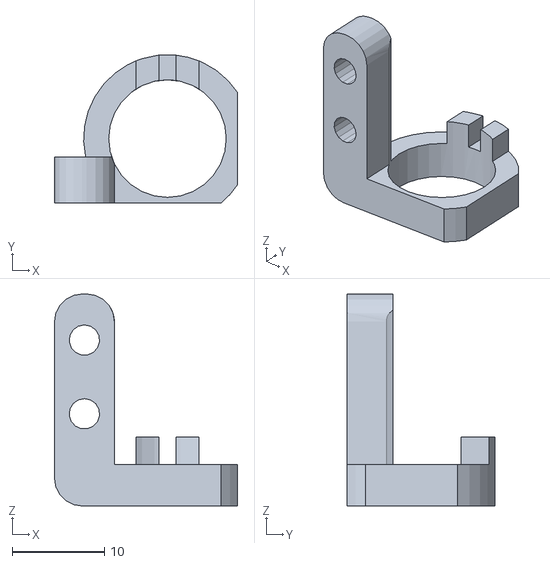
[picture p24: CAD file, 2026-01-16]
stl/control_panel/shut_off_mount.STL
19.9 x 16.1 x 23.0

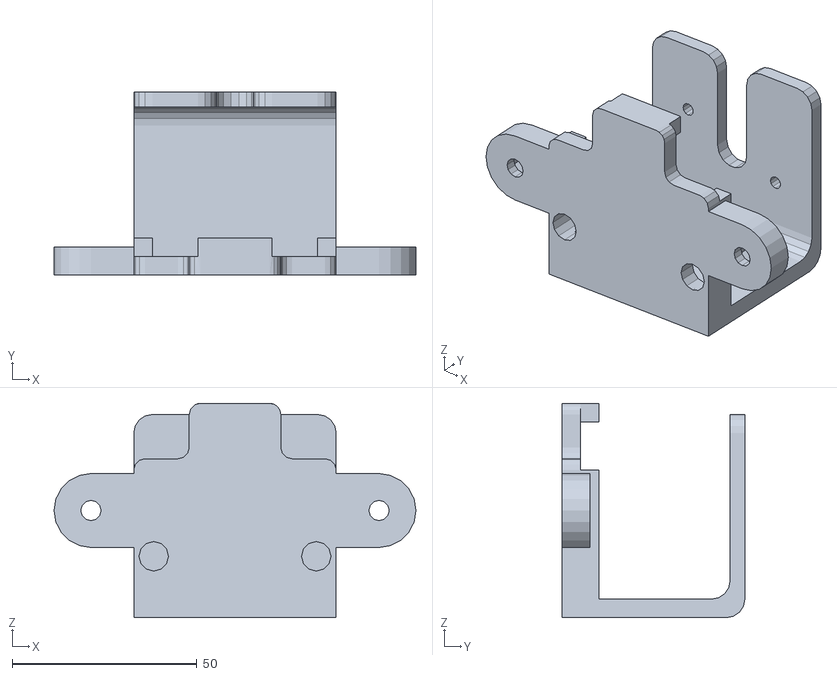
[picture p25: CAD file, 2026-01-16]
stl/electronics_plate/switch_mount.STL
98.0 x 49.5 x 58.0

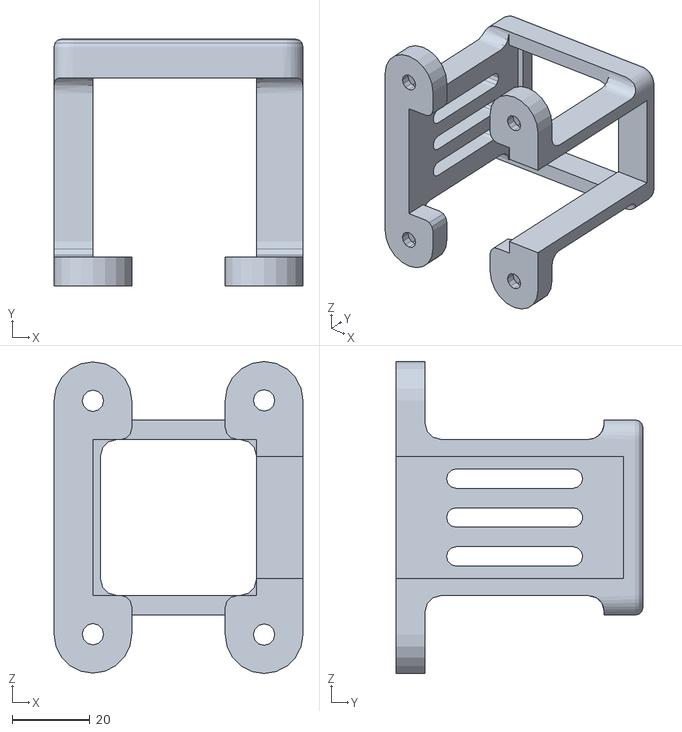
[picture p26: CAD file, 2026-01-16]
stl/pneumatic_mount/regulator_actuator_mounting.STL
64.0 x 63.5 x 80.2

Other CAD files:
stl/actuator_module/actuator_mount_top.STL
stl/actuator_module/actuator_mount_nozzle_holder.STL
stl/pneumatic_mount/regulator_levitation_mounting.STL
stl/actuator_module/actuator_mount_bottom.STL
stl/actuator_module/actuator_mount_holder.STL
stl/actuator_module/actuator_mount_holder_top.STL
stl/pneumatic_mount/bottle_conncet_bot_mid.STL
stl/pneumatic_mount/bottle_conncet_top_mid.STL
stl/pneumatic_mount/bottle_mount_hori.STL
stl/pneumatic_mount/bottle_mount_hori_top.STL

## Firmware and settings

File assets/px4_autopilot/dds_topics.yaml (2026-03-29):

#####
#
# This file maps all the topics that are to be used on the uXRCE-DDS client.
#
#####
publications:

  - topic: /fmu/out/battery_status
    type: px4_msgs::msg::BatteryStatus
    rate_limit: 1.

  # - topic: /fmu/out/sensor_combined
  #   type: px4_msgs::msg::SensorCombined

  - topic: /fmu/out/vehicle_angular_velocity
    type: px4_msgs::msg::VehicleAngularVelocity
    rate_limit: 50.

  - topic: /fmu/out/vehicle_attitude
    type: px4_msgs::msg::VehicleAttitude
    rate_limit: 50.

  - topic: /fmu/out/vehicle_control_mode
    type: px4_msgs::msg::VehicleControlMode
    rate_limit: 50.

  - topic: /fmu/out/vehicle_local_position
    type: px4_msgs::msg::VehicleLocalPosition
    rate_limit: 50.

  - topic: /fmu/out/vehicle_odometry
    type: px4_msgs::msg::VehicleOdometry
    rate_limit: 100.

  - topic: /fmu/out/vehicle_status
    type: px4_msgs::msg::VehicleStatus
    rate_limit: 5.

  - topic: /fmu/out/actuator_motors
    type: px4_msgs::msg::ActuatorMotors
    rate_limit: 50.

  - topic: /fmu/out/vehicle_torque_setpoint
    type: px4_msgs::msg::VehicleTorqueSetpoint
    rate_limit: 50.

  - topic: /fmu/out/vehicle_thrust_setpoint
    type: px4_msgs::msg::VehicleThrustSetpoint
    rate_limit: 50.

  # - topic: /fmu/out/log_message
  #   type: px4_msgs::msg::LogMessage

  # - topic: /fmu/out/mavlink_log
  #   type: px4_msgs::msg::MavlinkLog

  - topic: /fmu/out/rc_channels
    type: px4_msgs::msg::RcChannels
    rate_limit: 10.

  - topic: /fmu/out/vehicle_rates_setpoint
    type: px4_msgs::msg::VehicleRatesSetpoint
    rate_limit: 50.

  - topic: /fmu/out/vehicle_command
    type: px4_msgs::msg::VehicleCommand
    rate_limit: 50.

subscriptions:

  - topic: /fmu/in/arming_check_reply
    type: px4_msgs::msg::ArmingCheckReply

  - topic: /fmu/in/manual_control_input
    type: px4_msgs::msg::ManualControlSetpoint

  - topic: /fmu/in/offboard_control_mode
    type: px4_msgs::msg::OffboardControlMode

  - topic: /fmu/in/onboard_computer_status
    type: px4_msgs::msg::OnboardComputerStatus

  - topic: /fmu/in/telemetry_status
    type: px4_msgs::msg::TelemetryStatus

  - topic: /fmu/in/trajectory_setpoint
    type: px4_msgs::msg::TrajectorySetpoint

  - topic: /fmu/in/vehicle_attitude_setpoint
    type: px4_msgs::msg::VehicleAttitudeSetpoint

  - topic: /fmu/in/vehicle_rates_setpoint
    type: px4_msgs::msg::VehicleRatesSetpoint

  - topic: /fmu/in/vehicle_visual_odometry
    type: px4_msgs::msg::VehicleOdometry

  - topic: /fmu/in/vehicle_command
    type: px4_msgs::msg::VehicleCommand

  - topic: /fmu/in/vehicle_thrust_setpoint
    type: px4_msgs::msg::VehicleThrustSetpoint

  - topic: /fmu/in/vehicle_torque_setpoint
    type: px4_msgs::msg::VehicleTorqueSetpoint

  - topic: /fmu/in/actuator_motors
    type: px4_msgs::msg::ActuatorMotors

  - topic: /fmu/in/actuator_servos
    type: px4_msgs::msg::ActuatorServos

# Subscriptions multiplexed to uORB multi-instances (optionally demultiplexed based on a message field)
subscriptions_multi:
  # - topic: /fmu/in/aux_global_position
  #   type: px4_msgs::msg::AuxGlobalPosition
  #   route_field: id
  #   max_instances: 4

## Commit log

2026-01-16 init: release
    [actuation_plate.DXF, actuator_mount_bottom.STL, actuator_mount_holder.STL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]
2026-01-28 fix: STL filename
2026-02-20 feat: updated BOM with missing item
